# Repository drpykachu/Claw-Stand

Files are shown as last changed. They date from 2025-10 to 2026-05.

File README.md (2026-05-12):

#  Claw Stand

## Hello all! 

This project is inspired by the **BattleBots claw stand robot**:

<div align="center">
  BATTLEBOTS
</div>

---

## Part 1: Mathematical Model

Each finger in the claw contains **3 motors** — **Motor A**, **Motor B**, and **Motor C**.  
Each motor rotates by an angle:  
- Motor A → $\theta_a$  
- Motor B → $\theta_b$  
- Motor C → $\theta_c$  

We need to perform **inverse kinematics** to find the angles needed to position the finger tip at a given **3D coordinate**:

$$(X_p, Y_p, Z_p)$$

<div align="center">
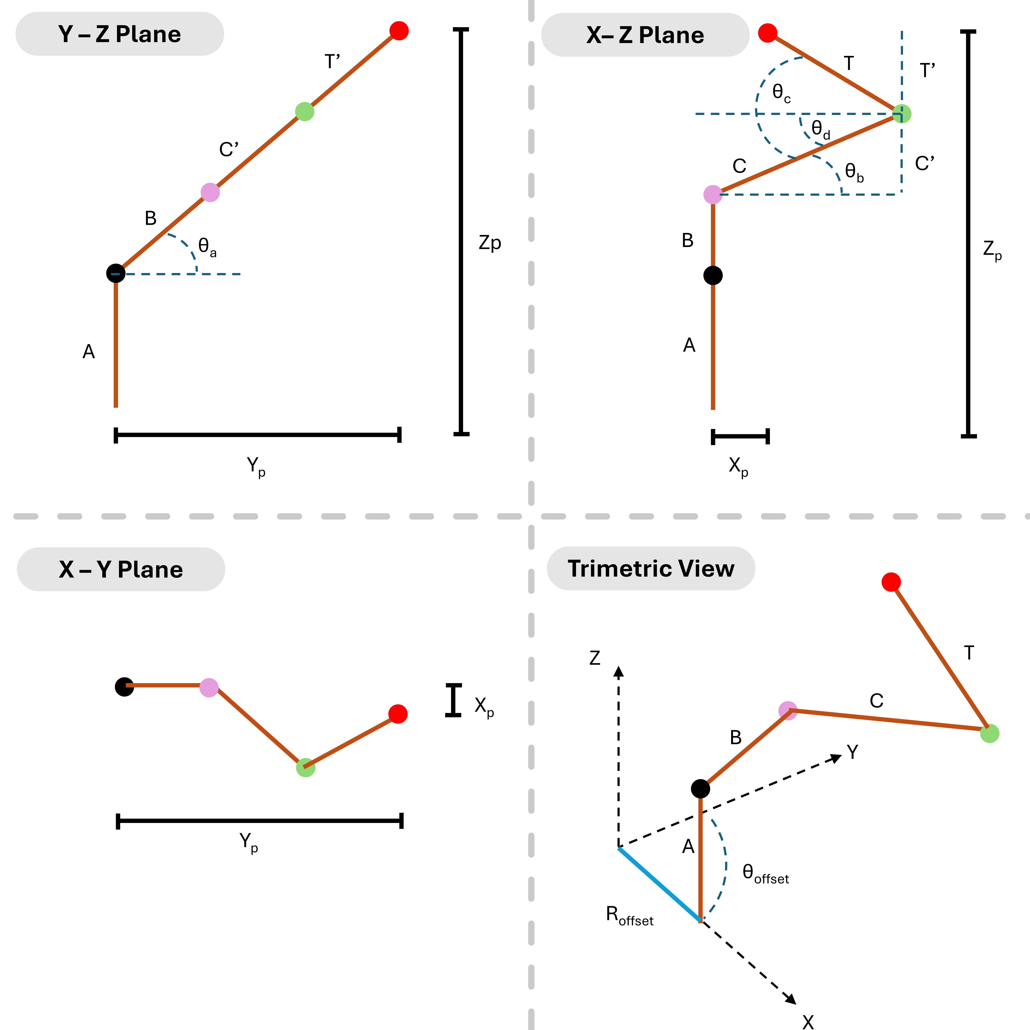
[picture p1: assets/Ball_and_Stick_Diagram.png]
Diagram
  
</div>

---

## Equation Setup

We’re going from a target point in space $(X_p, Y_p, Z_p)$ to joint angles $(\theta_a, \theta_b, \theta_c)$.

$$
\angle AB = \theta_a \quad \angle BC = \theta_b \quad \angle CT = \theta_c
$$

We also define:

$$
\theta_d = \theta_b - \theta_c
$$

---

### Deriving $Z_p$

$$
Z_p = B\sin\theta_a + C'\sin\theta_a + T'\sin\theta_a + A
$$

Substitute: $C' = C\sin\theta_b, \quad T' = T\sin\theta_d $

So:

$$
\boxed{Z_p = B\sin\theta_a + C\sin\theta_b\sin\theta_a + T\sin\theta_d\sin\theta_a + A} \quad \text{(Eq. 1)}
$$

---

### Deriving $Y_p$

$$
Y_p = B\cos\theta_a + C'\cos\theta_a + T'\cos\theta_a
$$

Substitute: $C' = C\sin\theta_b, \quad T' = T\sin\theta_d$

So:

$$
\boxed{Y_p = B\cos\theta_a + C\sin\theta_b\cos\theta_a + T\sin\theta_d\cos\theta_a} \quad \text{(Eq. 2)}
$$

---

### Deriving $X_p$

$$
\boxed{X_p = C\cos\theta_b + T\cos\theta_d} \quad \text{(Eq. 3)}
$$

---

## Step 1 — Solving for $\theta_a$

Visually, this is true from Eq. (1) and Eq. (2):

$$
\tan\theta_a = \frac{Z_p - A}{Y_p}
$$

So:

$$
\theta_a = atan2(\frac{Z_p - A}{Y_p})
$$

#### *Note: atan2 provides the quadrant and is used here, as atan loses information regarding negatives and associated quadrants.
---

## Step 2 — Solving for $\theta_b$ and $\theta_d$

We now solve for $\theta_b$ and $\theta_d$, given:

$$
Y_p = B\cos\theta_a + C\sin\theta_b\cos\theta_a + T\sin\theta_d\cos\theta_a,
$$

$$
X_p = C\cos\theta_b + T\cos\theta_d.
$$

---

### Step 1 — Simplify the equations

Divide the first equation by $\cos\theta_a$ (assuming $\cos\theta_a \neq 0$) and define:

$$
S = \frac{Y_p}{\cos\theta_a} - B.
$$

Then the system becomes:

$$
C\sin\theta_b + T\sin\theta_d = S,  
$$

$$
C\cos\theta_b + T\cos\theta_d = X_p.
$$

---

### Step 2 — Interpret geometrically

These equations represent a **vector addition** in the plane:

$$
C e^{i\theta_b} + T e^{i\theta_d} = X_p + iS \equiv R e^{i\phi},
$$

where

$$
R = \sqrt{X_p^2 + S^2}, \quad \phi = atan2(\frac{S}{X_p}).
$$

---

### Step 3 — Eliminate $\theta_d$

Using the magnitude condition for the complex sum, we find:

$$
X_p\cos\theta_b + S\sin\theta_b = K,
$$

where

$$
K = \frac{R^2 + C^2 - T^2}{2C}.
$$

Let $A = X_p$, $B = S$, and $R = \sqrt{A^2 + B^2}$.
  
Then:

$$
A\cos\theta_b + B\sin\theta_b = K
$$

can be rewritten as:

$$
R\cos(\theta_b - \phi) = K.
$$

---

### Step 4 — Solve for $\theta_b$

$$
\boxed{\theta_b = \phi \pm \arccos\left(\frac{K}{R}\right)}
$$

Feasibility condition:

$$
\left|\frac{K}{R}\right| \le 1.
$$

If \(|K/R| > 1\), no real solution exists.

---

### Step 5 — Solve for $\theta_d$

For each valid $\theta_b$:

$$
\cos\theta_d = \frac{X_p - C\cos\theta_b}{T}
$$

$$
\sin\theta_d = \frac{S - C\sin\theta_b}{T}
$$

$$
\boxed{\theta_d = atan2(\frac{\sin\theta_d}{ \cos\theta_d})}.
$$

---

### Step 6 — Boundary Condition

The result of $\theta_b$ and $\theta_d$ can yield more than one solution. To guarantee that the joints bend outward:

$$
\theta_d > \theta_b
$$

Remembering that $\theta_d = \theta_b - \theta_c$ and substituting:

$$
\theta_c > 0
$$

guarantees a single solution.

---

### Step 7 — Python Implementation

```python
import numpy as np

def solve_thetas(Zp, Yp, Xp, A, B, C, T, Offset_R):
    """Returns the angles (in radians) of motors to obtain a point in space (Xp, Yp, Zp)"""
    Xp = Xp - Offset_R
    Yp = Yp

    # Helps with breakdown of atan2 at infinity as Yp -> 0
    if Yp < 0.0005 and Yp > 0:
        Yp = 0.0005        
    if Yp > -0.0005 and Yp <= 0:
        Yp = -0.0005

    theta_a = np.atan2((Zp-A),Yp)
    ca = np.cos(theta_a)
    
    S = Yp/ca - B
    R = np.hypot(Xp, S)           # sqrt(Xp^2 + S^2)
    phi = np.arctan2(S, Xp)
    K = (R*R + C*C - T*T) / (2.0*C)

    if abs(K/R) > 1.0 + 1e-12:
        return []  # no real solutions

    # clamp for numeric stability
    val = np.clip(K/R, -1.0, 1.0)
    acos_val = np.arccos(val)

    thetab_solutions = [phi + acos_val, phi - acos_val]
    solutions = []
    for tb in thetab_solutions:
        cb = np.cos(tb); sb = np.sin(tb)
        cd = (Xp - C*cb) / T
        sd = (S  - C*sb) / T
        # numeric clamp
        cd = np.clip(cd, -1.0, 1.0)
        sd = np.clip(sd, -1.0, 1.0)
        td = np.arctan2(sd, cd)

        # ensures only one solution
        tc = td - tb

        if tc > 0:
            solutions.append((theta_a, tb, td))
            
    return solutions

```

### Python Model Implementation 

[Model Source Code](https://github.com/drpykachu/Claw-Stand/blob/main/Edition%20V2.0%20-%20Stepper%20Motor/Software/Python/Windows%20-%20Claw%20Stick%20Model%20V2.2.py)

<div align="center">
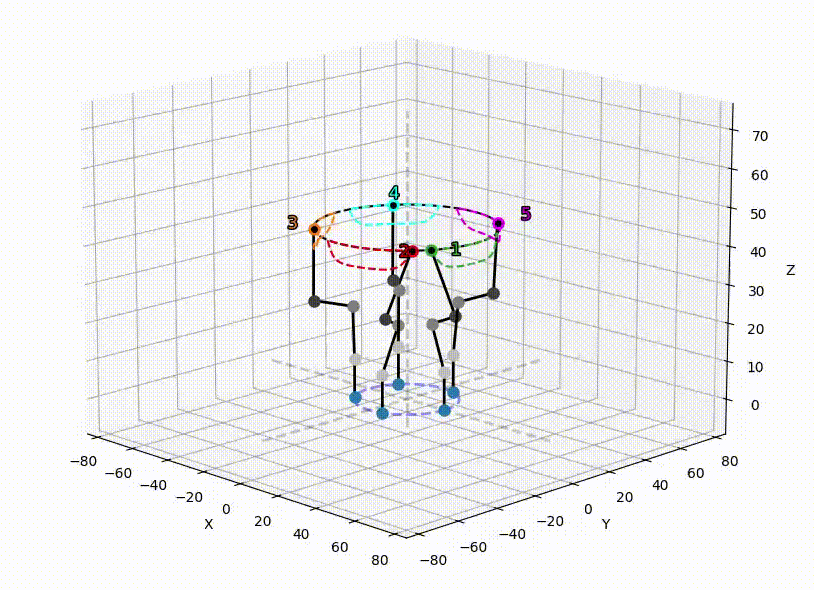
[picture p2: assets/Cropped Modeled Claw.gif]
Python Model
  
</div>

---

## Part 2: Hardware Selection

The angles needed for reaching a point in (x,y,z) space is now fully defined with the mathematical model. However, more thought is needed for selecting the hardware for turning the mathematicl model into a working phyiscal model

---
### The Motor:

There are several classes of motor that were considered, but servo motors are chosen as the range of movement (<180°), built-in rotary encoder (for position tracking and tuning with PID), and step accuracy (the smaller the better) are ideal. Several makes and models of servo motors were evaluated:

* [S8218 High Speed servo](https://www.cysmodel.com/products/cys-s8218-40kg-digital-metal-gear-servo/)
* [SC09 Series Serial Bus Servo](https://www.waveshare.com/SC09-Servo.htm)
* [ST3215 Series Serial Bus Servo](https://www.waveshare.com/st3215-servo.htm?srsltid=AfmBOorEyoYq279kdzu4ZvWRVoV5O3Idv0StNNJXvp_PE0Ioi92Gx9X2)

### Servo Motor Criteria

The three most important criteria for the servo motors to ensure a success build are as follows:

1. Small step angle (as well as compact)
2. Strength requirement (to hold at least coffee mug)

### Step Angle

The Ball-And-Stick model has the oversight of showing us how the model would react with perfect decimal-point accuracy. In the real world, motors have an angle, the step angle or resolution angle, of how small they can exert movement in discrete steps. For instance, a large step can lead to unwanted behavior. A Computer Aided Design (CAD) was built for the SC09 motors, where the components were designed in mind for 3D printing later on. The model with a 2° step is seen here (notice the choppiness and inaccurate positioning on the the wanted path):

<div style="display: flex; justify-content: center;">
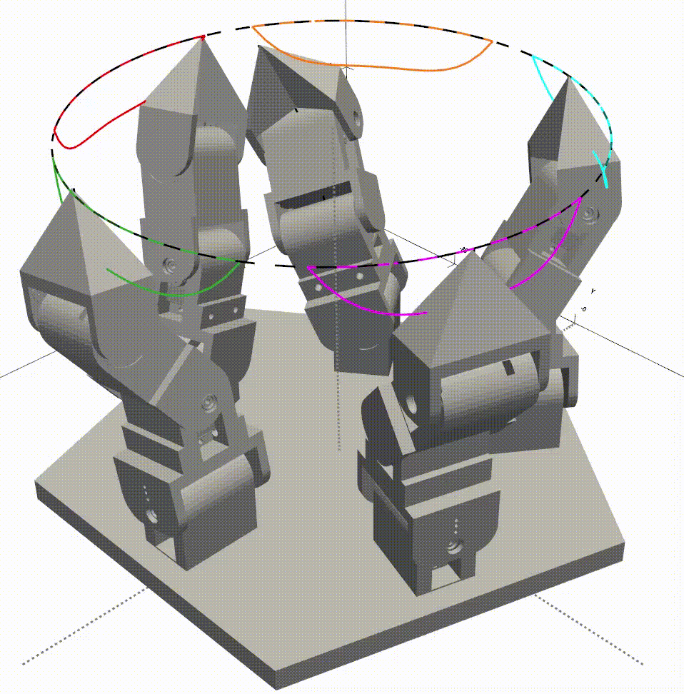
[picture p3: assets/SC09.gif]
  
</div>

<br>

Choppiness and innacuracy of the fingers is seen, indicating that there will be poor movement and stability. A smaller step angle is needed to ensure smooth control. 

The smallest step angle size and  10x step angle size (closer to actual movement due to internal deadband settings), is seen for each motor below:

| Make | Min Step Size  | Acutal Step Size | 
|---|---|---|
| S8218 | 0.360 | 3.60 |
| SC09 | 0.293 | 2.93 | 
| ST3215  | 0.088 | 0.88 |

A CAD model for the ST3215 was to show the operation for a 0.88° step angle, where much better control smoothness is observed:

<div style="display: flex; justify-content: center;">
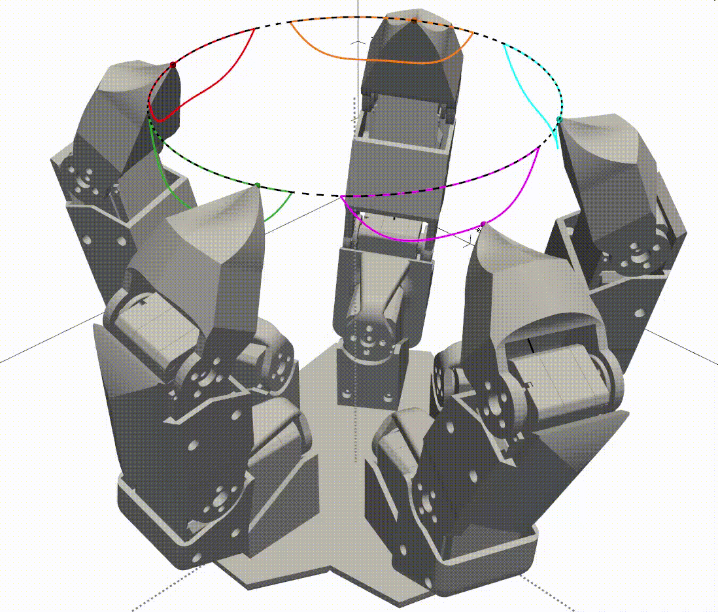
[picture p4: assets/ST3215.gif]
  
</div>

The S8218 and SC09 motors were no longer considered as they show poor control for this configuration.

### Strength Requirement
The ST3215 achieves its positional accuracy by using a gearbox. Gearboxes are good for increasing torque (strength) and increasing position resolution, but they are bad because they introduce *backlash*. Backlash is the clearance or lost motion in a mechanism caused by gaps between the parts. If there was no clearance between the gears, any anamoly would cause the gearbox to seize - causing lack or no motion and potential motor failure; so some backlash is desired. However, backlash in this system means that the rotor can move without the output shaft moving, causing a displacement between the modeled position and the actual position (*bad*).

Here is a picture depicting backlash:

<div align="center">
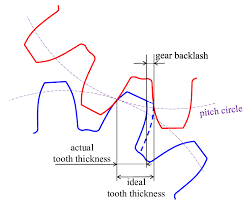
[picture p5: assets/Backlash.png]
Backlash
  
</div>

Only one side of the gear teeth is engaged at a time. Once the gears spin the other direction, there will be a moment in time (and space) where the contact has to shift from one side to the other. However, if a sufficient amount of external torque is applied, one side of the gear will be engaged at all times - and therefore eliminating backlash.

Looking at bottom motor (Motor A) for example, gravity will pull the gearings to one side, until 90 degrees, where it will slop over to the other side. Assigning positive torque to a clockwise direction (and thus a negative torque is counter clockwise), the moment ($\tau$) associated for each motor is found as:

$$\tau = \sum_{i=1}^{n} l_i·m_i·g·cos(\theta) + l_L·m_L·g·cos(\theta); $$

$$\tau_C = [T·(m_{p,T})]·g·cos(\theta) + T·m_L·g·cos(\theta)$$

$$\tau_B = [T·(m_{p,T}) + (T+C)·(m_{p,T}+m_{p,C}+m_{m})]·g·cos(\theta) + (T+C)·m_L·g·cos(\theta)$$

$$\tau_A = [T·(m_{p,T}) + (T+C)·(m_{p,T}+m_{p,C}+m_{m}) + (T+C+B)·(m_{p,T}+m_{p,C}+m_{p,B}+ 2m_{m})]·g·cos(\theta) + (T+C+B)·m_L·g·cos(\theta) $$

where $l_i$ is arm length, $l_L$ is load length, $m_{p}$ is mass of plastic, $m_{m}$ is mass of motor, $m_{L}$ is mass of load, and $g$ is gravity. Note that the moments $\tau_B$ and $\tau_A$ are taken as worst-case scenarios of the finger being fully extended.

The torque vs. angle behavior, where the load is only applied during contact with the plate,
is seen here: 

<div align="center">
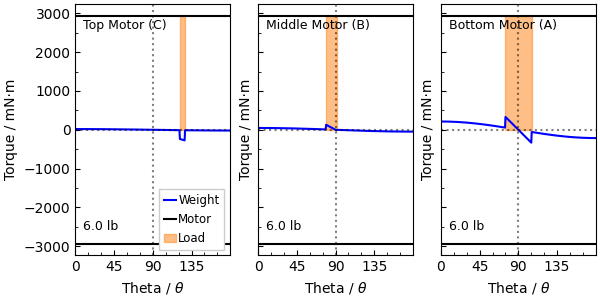
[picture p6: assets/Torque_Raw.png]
Torque_Raw
  
</div>

My father chimed in at this point to point out that the torque measurment only needs to be considered for motors that have angles cross the 90° mark. This agrees with the point that as long there is no change in sign (+/-) of torque, there is no switch over from one gearing side to the other. Thus, motors C and B are removed from further analysis.

An additional torque will be needed to have the gears stay on one side for motor A. A torsion spring will be added to raise the torqe as a function of the angle, with the relationship seen as:

$$\tau_S = K_s\theta$$

The torque increased with the angle moved (assuming a 270° spring deflection) so that the gears are preloaded the angle reaches 90°. The torque behavior with the added spring is seen as:

<div align="center">
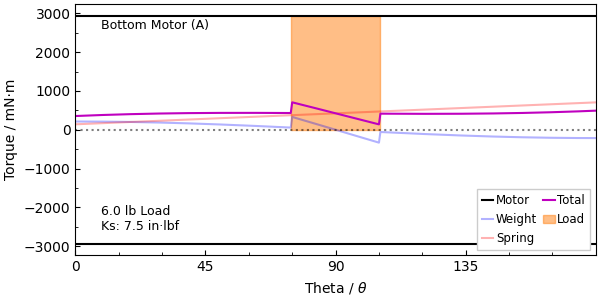
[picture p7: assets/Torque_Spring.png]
Torque_Spring
  
</div>

The torque is now brought to one side (positive) and remains there for all angles - ensuring that the gears are continuously in contact. Motors A, B, and C are now fully defined. The final model to include the spring hardware (near the bottom, as only motor A needs it) is seen here:

<div style="display: flex; justify-content: center;">
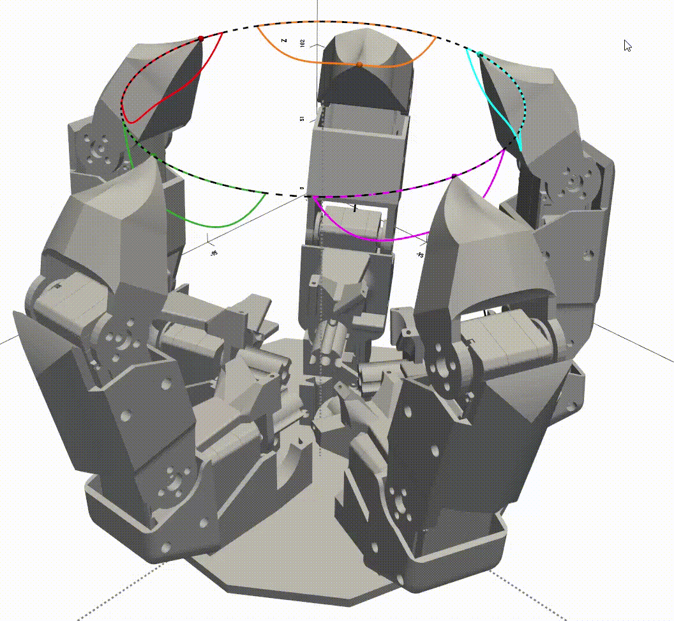
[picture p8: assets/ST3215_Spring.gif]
  
</div>

## Part 3: Final Build And Considerations

The translation from theoretical model, to CAD model, to 3D printing and fine-tuning took a considerable amount of time and effort. The considerations for electronics, wiring, polishing, machining, soldering, and coding are not shown here, simply because it is not worth the time and effort type of out the explanations for each aspect. Rather, I wanted to share the aspects to which I thought were the neat.

### Electronics Bay

The fingers that comprise the claw in the presented animations are connectec to a base plate. I chose to make an electronics bay that houses the computer, power supplies, and other ancillary electronics equipment to make the claw a stand-alone piece. The processor chosen to run the claw computations and motor control commands is a Easpberry Pi 5. The motor driver is a 12v serial bus driver. The Pi requires a 5V power supply, and the motor driver require a 12V supply, which are included in the bay as well. Lastly, I included a ring of LED that is oriented upwards to illuminate the object being held. 

<div align="center">
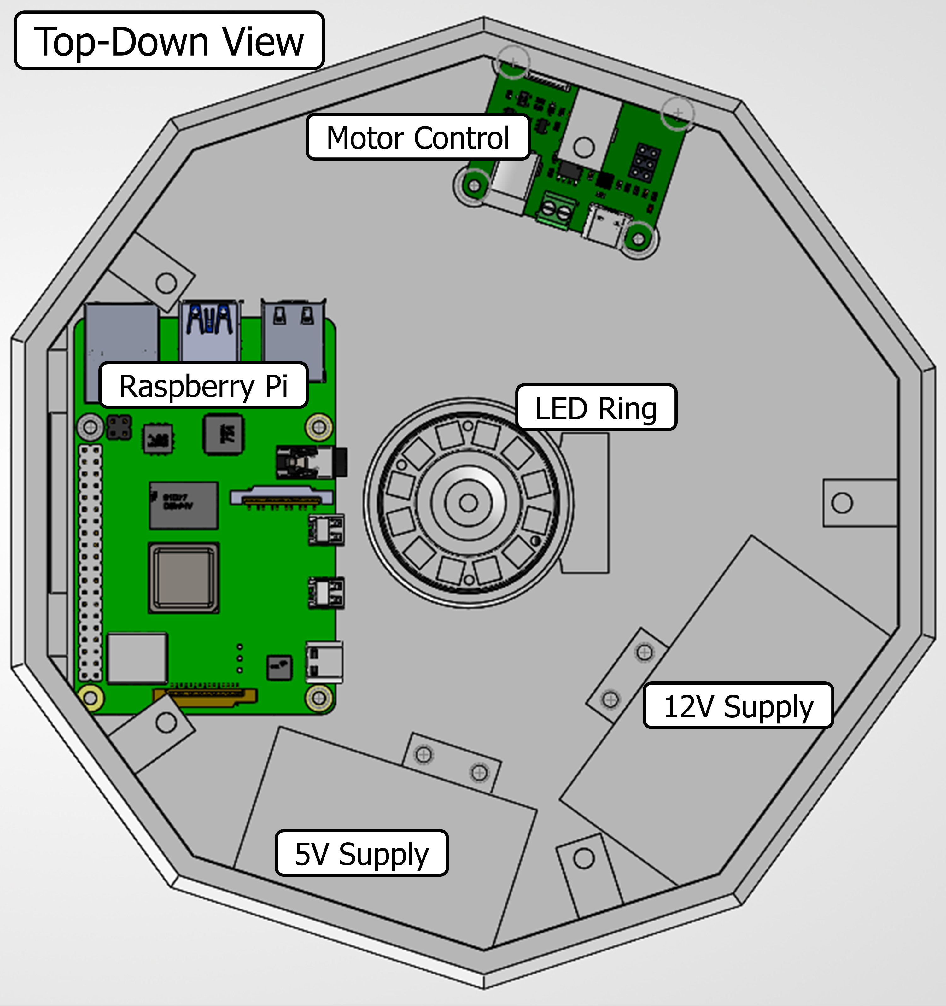
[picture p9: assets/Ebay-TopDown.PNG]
Ebay-TopDown
  
</div>
 
<br>
<div align="center">
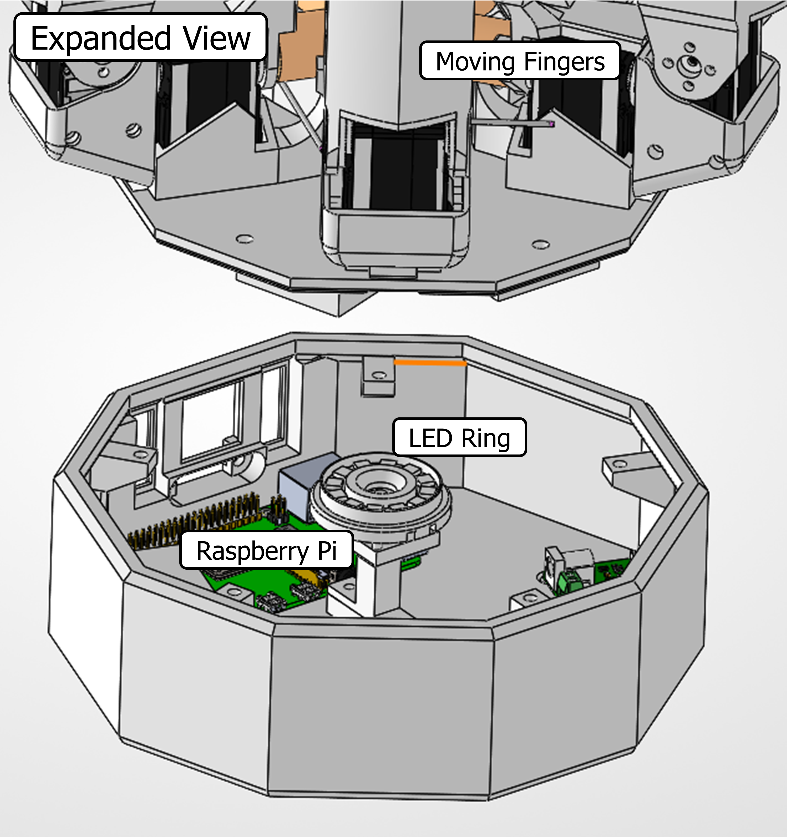
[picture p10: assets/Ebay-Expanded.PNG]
Ebay-Expanded
  
</div> 

<br>

### Camera-Plate Feedback Loop

The claw, finally completed and ready to run, was initially only able to hold spherical objects as they are symmetrical in any orientation. Any spherical object would auto-correct if there was any mis-calibration in fingertip position. Holding other types of objects, such as flat objects (plate), would be a challenge as any fingertip position mis-calibration would lead to drift. Enough drift, and the plate falls off the plate. With the addition of a small raspberry pi camera, along with the processing power of the Raspberry Pi and the ulimtation aspect of the LED ring, image processing feedback loop was developed to track the location of plate. If the plate drifted too far to one side, the raspberry pi goes into "fixing mode" to bring the plate back to near center. *Development of this image correction hardware and software took by far the longest amound of time to make*

The animation of a drift detection and correction is seen here:

<div style="display: flex; justify-content: center;">
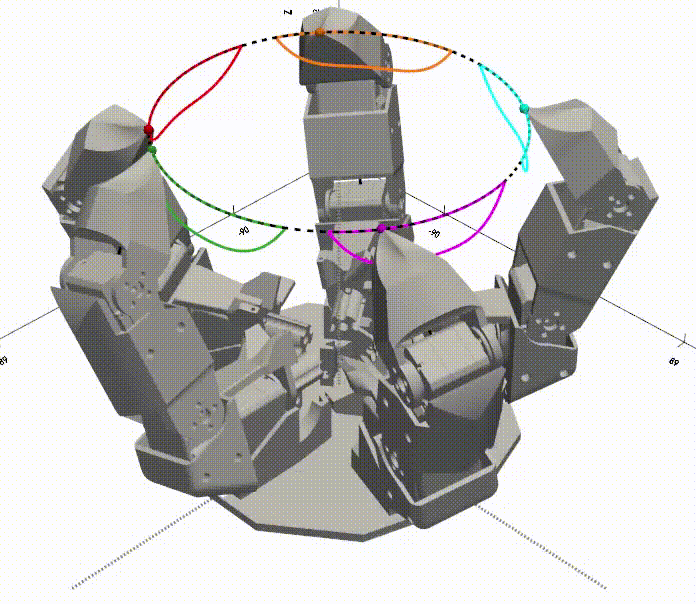
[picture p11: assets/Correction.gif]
Correction
  
</div>

<br>
Where the dashed black line is the normal path to follow, and the gray curve is the correction path. When a drift threshold is met (15 mm from center), the all fingers move in sync to move the plate back to the center. After the translational movement, the fingers need to reset their position from the correction path to the normal path. I first attempted to hold each finger still and move one at a time, but there were instances of imbalance between fingers due to the position on the path, and the the plate would fall off. The resetting of the fingers in this animation differs from the former by having the finger position reset during the downsweep. This is observed by a finger leaving on the dashed gray circle during the start of the downsweep, and touching the dashed black circle on the end of the downsweep.

## Gallery

### Electronics Bay

<div align="center">
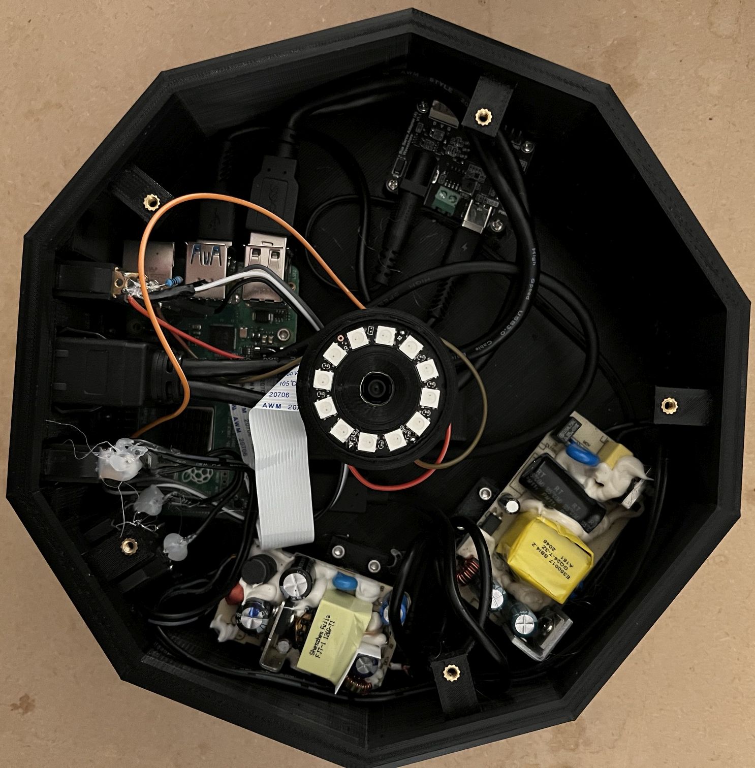
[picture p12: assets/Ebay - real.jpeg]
Ebay-real
  
</div> 

<br>

### Claw - Stagnant

<div align="center">
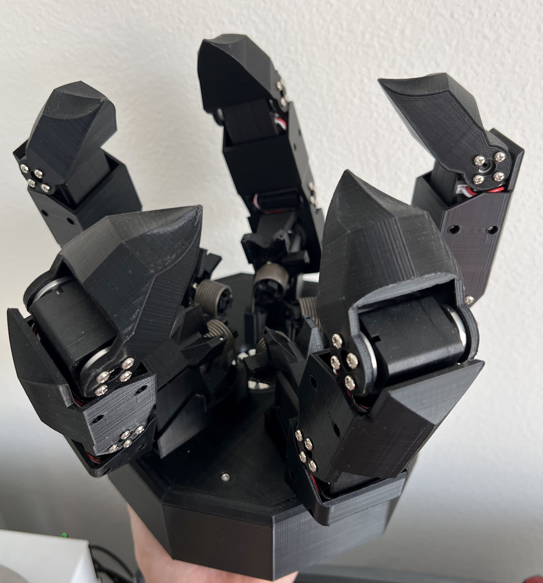
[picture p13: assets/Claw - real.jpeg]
Claw-real
  
</div> 

<br>

### Claw - Moving

<br>

https://github.com/user-attachments/assets/a1c54686-66d3-4b85-84ab-2f56ab6c1aae

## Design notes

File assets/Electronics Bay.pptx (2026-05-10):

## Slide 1

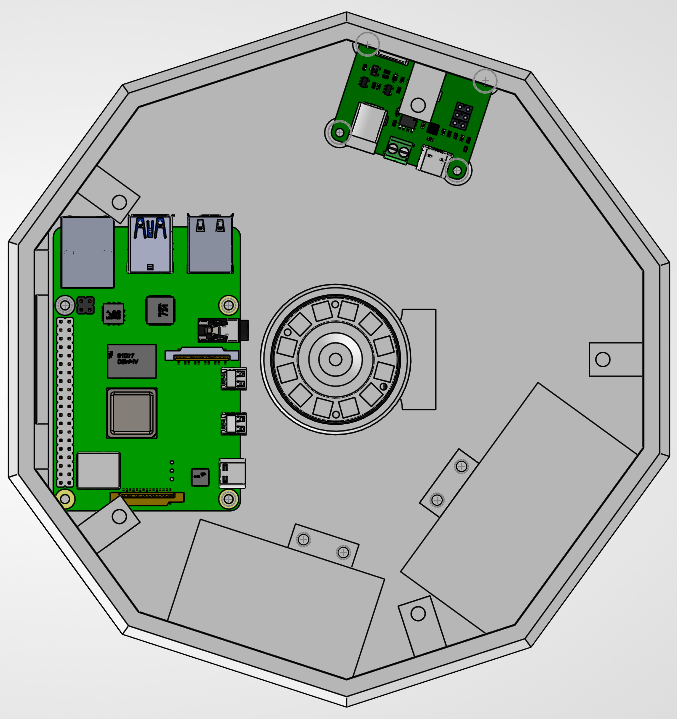
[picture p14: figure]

Top-Down View

Motor Control

Raspberry Pi

LED Ring

12V Supply

5V Supply

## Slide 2

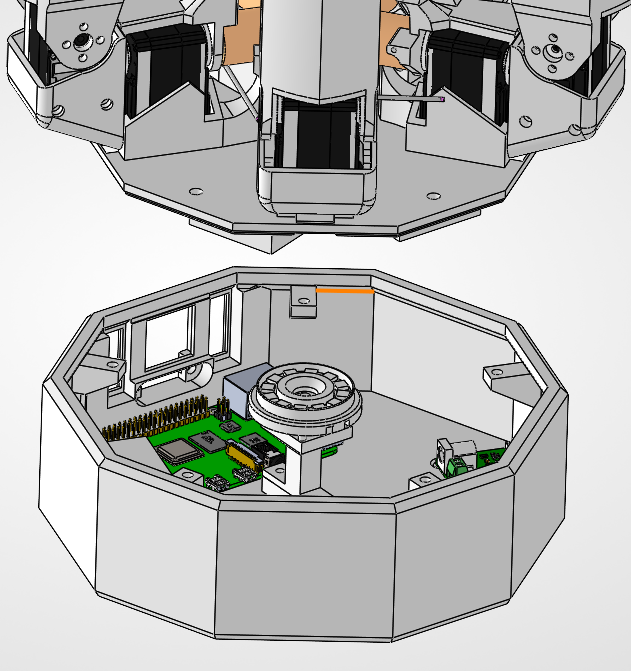
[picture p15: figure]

Expanded View

Moving Fingers

LED Ring

Raspberry Pi

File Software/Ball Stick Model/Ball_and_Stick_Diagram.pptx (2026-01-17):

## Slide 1

Y – Z Plane

T’

X– Z Plane

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
X – Y Plane

Trimetric View

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
θoffset

Roffset

X

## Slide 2

Y – Z Plane

T’

X– Z Plane

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
X – Y Plane

Trimetric View

Yp

Z

T

Xp

θoffset

B

Y

C

A

Roffset

X

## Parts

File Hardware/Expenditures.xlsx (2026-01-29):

Index | Item | Amount needed | Quantity in Unit | Units needed | Cost per unit | Total Cost | Item Type | Used in Final | Link
1 | Raspberry Pi 4 Model B Kit | 1 | 1 | 1 | 119.99 | 119.99 | Logic | Yes | https://www.amazon.com/dp/B07XTQL6YZ?ref=ppx_yo2ov_dt_b_fed_asin_title&th=1
2 | Raspberry Pi Camera Module 3 | 1 | 1 | 1 | 18.5 | 18.5 | Logic | Yes | https://www.amazon.com/Arducam-Raspberry-Camera-Autofocus-15-22pin/dp/B0C9PYCV9S
3 | Powered USB Hub (<3 ports) | 1 | 1 | 1 | 7.99 | 7.99 | Logic | No | https://www.amazon.com/RSHTECH-Splitter-Portable-Aluminum-Individual/dp/B07HMZSRS7
4 | ESP32 DevkitC | 1 | 3 | 1 | 17.97 | 17.97 | Logic | Yes | https://www.amazon.com/ESP32-DevKitC-32-Development-Supporting-Bluetooth-Interface/dp/B0DYDN5X1Z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
5 | USB C cables | 1 | 5 | 1 | 7.99 | 7.99 | Logic | No | https://www.amazon.com/Android-Compatible-Smartphones-Charging-Stations/dp/B095JZSHXQ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
6 | 28BYJ-48 ULN2003 5V Stepper Motor + ULN2003 | 5 | 5 | 1 | 14.99 | 14.99 | Motor | No | https://www.amazon.com/28BYJ-48-ULN2003-Stepper-Driver-Arduino/dp/B07YRHX73L
7 | Female to Female Breadboard Jumper Wires | 120 | 120 | 1 | 7.98 | 7.98 | Motor | No | https://www.amazon.com/dp/B07GCY6CH7?ref=ppx_yo2ov_dt_b_fed_asin_title
8 | 5 V 8–10 A Regulated DC Power Supply | 1 | 1 | 1 | 14.99 | 14.99 | Power | No | https://www.amazon.com/PHEVOS-Universal-Switching-Raspberry-Computer/dp/B07H5Q2PC2?hvadid=694085195674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
9 | PSU Capacitor | 1 | 2 | 1 | 7.99 | 7.99 | Power | No | https://www.amazon.com/Cermant-100v-3-3uf-Electrolytic-Non-Polarized/dp/B0CZP2Q26M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
10 | C14 Panel Mount Plug Adapter | 1 | 2 | 1 | 7.79 | 7.79 | Power | Yes | https://www.amazon.com/dp/B07PVP7GL2?ref=ppx_yo2ov_dt_b_fed_asin_title&th=1
11 | 4-40 bolts | 5 | 100 | 1 | 6.27 | 6.27 | Structure | Yes | https://www.amazon.com/dp/B0F93L5MJK?ref=ppx_yo2ov_dt_b_fed_asin_title
12 | 4-40 threaded inserts | 5 | 100 | 1 | 11.02 | 11.02 | Structure | Yes | https://www.amazon.com/dp/B0DY6P1K41?ref=ppx_yo2ov_dt_b_fed_asin_title
13 | 12V power supply | 1 | 1 | 1 | 8.46 | 8.46 | Power | Yes | https://www.amazon.com/dp/B0D476TCVW?ref=ppx_yo2ov_dt_b_fed_asin_title
14 | Stepper motor driver | 1 | 1 | 1 | 13.23 | 13.23 | Motor | No | https://www.amazon.com/dp/B0CP92T4QR?ref=ppx_yo2ov_dt_b_fed_asin_title
15 | Stepper motor driver | 1 | 1 | 1 | 17.64 | 17.64 | Motor | No | https://www.amazon.com/dp/B0832SK397?ref=ppx_yo2ov_dt_b_fed_asin_title
16 | Power supply adjustable | 1 | 1 | 1 | 48.21 | 48.21 | Tool | No | https://www.amazon.com/dp/B0D2TLJP3D?ref=ppx_yo2ov_dt_b_fed_asin_title
17 | Flanged bushings | 1 | 1 | 1 | 7.16 | 7.16 | Structure | No | https://www.amazon.com/dp/B0FHQ63MS3?ref=ppx_yo2ov_dt_b_fed_asin_title
18 | ST09 Servos | 3 | 1 | 3 | 15.99 | 47.97 | Motor | No | https://www.amazon.com/dp/B0C3QGLGB8?ref=ppx_yo2ov_dt_b_fed_asin_title
19 | Servo driver | 1 | 1 | 1 | 19.19 | 19.19 | Logic | Yes | https://www.amazon.com/dp/B0D1R4SGFS?ref=ppx_yo2ov_dt_b_fed_asin_title&th=1
20 | ST3215 Servo | 15 | 1 | 15 | 26.99 | 404.85 | Motor | Yes | https://www.amazon.com/dp/B0FKY4Z15R?ref=ppx_yo2ov_dt_b_fed_asin_title
21 | PLA Filament | 1 | 1 | 1 | 14.91 | 14.91 | Structure | Yes | https://www.amazon.com/your-orders/orders?startIndex=0&ref_=ppx_yo2ov_dt_b_pagination_2_1
 |  | Breakdown:
 |  | Category | Cost
 |  | Logic | 191.63
 |  | Motor | 506.66
 |  | Power | 39.23
 |  | Structure | 39.36
 |  | Tool | 48.21
 |  | Total | 825.09
 |  | Perfect | 628.95
 |  | Learning | 196.14

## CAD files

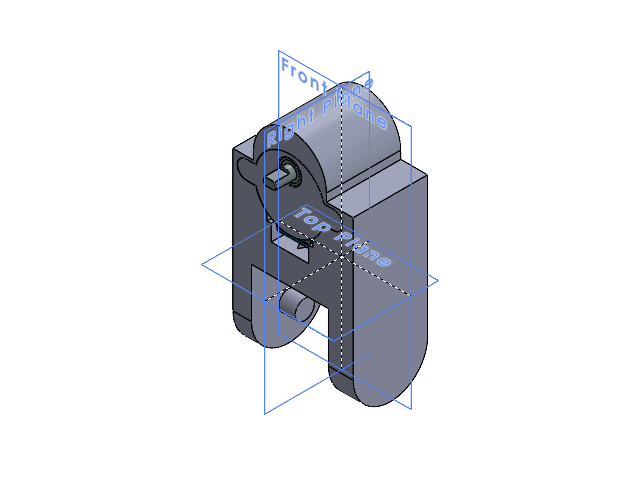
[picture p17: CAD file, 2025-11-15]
Hardware/3D Models/28BYJ-48/Sub Assemblies/Motor B + bearing.SLDASM
Motor B
Bearing
28BYJ-48
Motor Holder
Bearing Insert

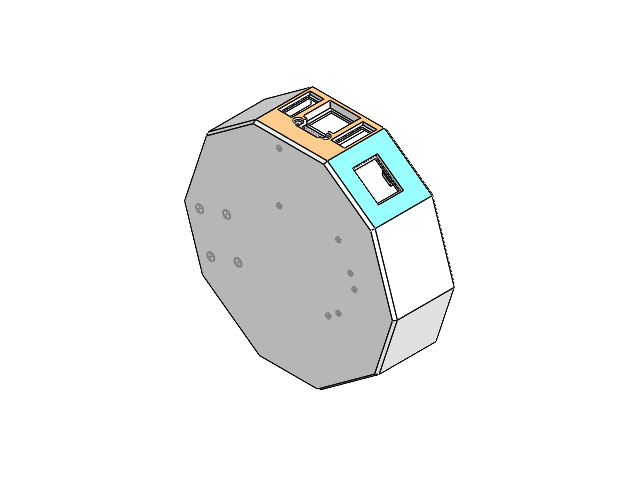
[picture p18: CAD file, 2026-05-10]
Hardware/3D Models/ST3215/V1.0/ST3215_Assembly_Electronics_Bay.SLDASM
ST3215_Electronics_Bay
5V_Supply
5V_Base_Connector
12V_Base_Connector
12V_Supply
Bus Servo Adapter (A)
Raspberry Pi 4 Model B
Camera_Base_Glue
Camera_Base_Screw
arducam
Camera_Hole
WS2812 LED Ring

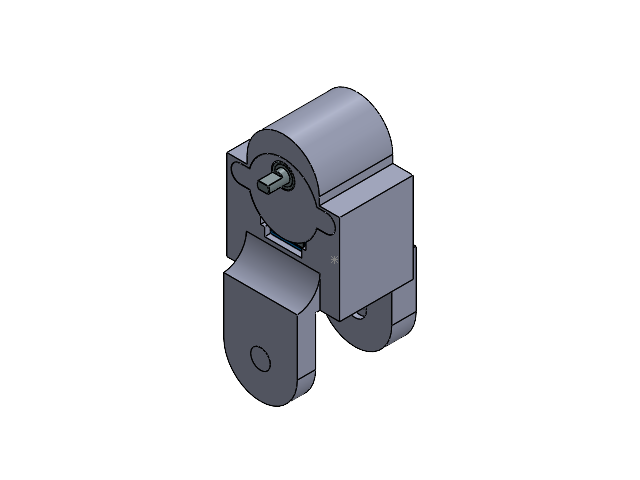
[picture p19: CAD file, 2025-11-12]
Hardware/3D Models/28BYJ-48/Sub Assemblies/Motor C + bearing.SLDASM
Motor C
28BYJ-48
Bearing
Motor Holder

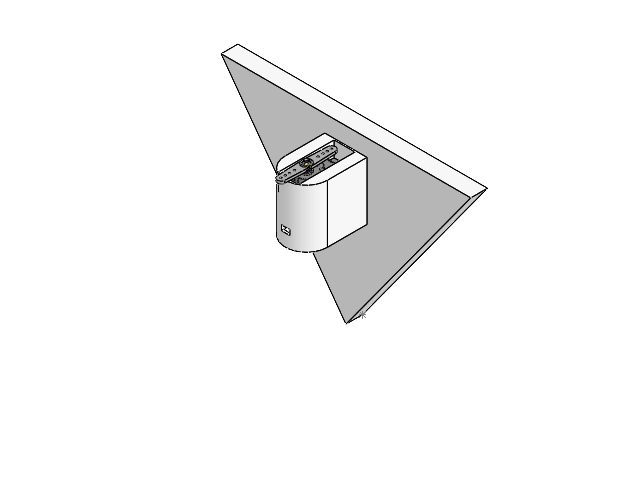
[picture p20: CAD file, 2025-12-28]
Hardware/3D Models/SC09/V0.1 - Bearing/SC09_Holder_Motor_A_Python.SLDASM
SC09_Holder_Motor_A
SC09-SERVO
SC09_Servo_Connector

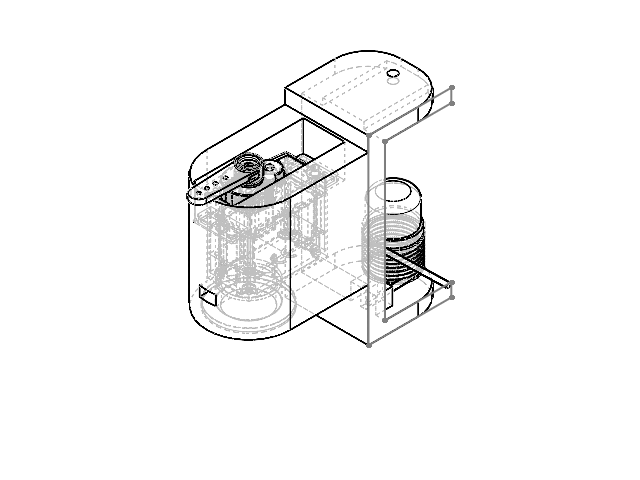
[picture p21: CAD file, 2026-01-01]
Hardware/3D Models/SC09/V0.2 - Bushing & Spring/SC09_Holder_Motor_C_Python.SLDASM
SC09-SERVO
SC09_Servo_Connector
SC09_Holder_Motor_C
9271K382_Torsion Spring
Bushing

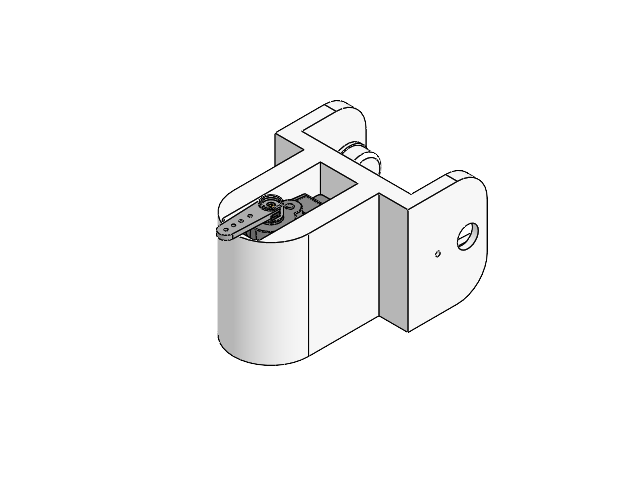
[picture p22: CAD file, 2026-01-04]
Hardware/3D Models/SC09/V0.2 - Bushing/SC09_Holder_Motor_B_Python.SLDASM
SC09-SERVO
SC09_Servo_Connector
SC09_Holder_Motor_B
Bushing

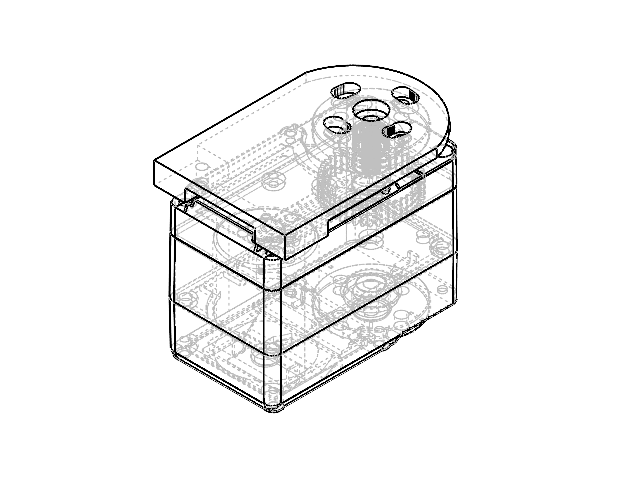
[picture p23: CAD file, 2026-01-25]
Hardware/3D Models/ST3215/Motor Debugging/CenterFinder_Test.SLDASM
CenterFinder
ST3215

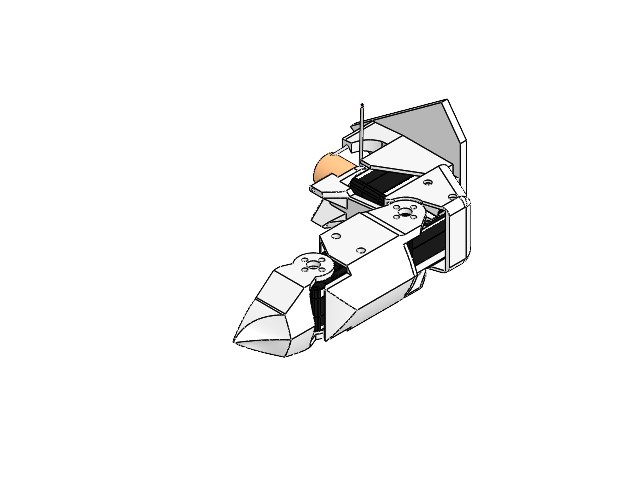
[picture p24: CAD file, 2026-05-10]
Hardware/3D Models/ST3215/V1.0/ST3215_Assembly_Finger.SLDASM
ST3215_Holder_A
ST3215 x 3
ST3215_Holder_B
ST3215_Holder_C
ST3215_Holder_A_Arm_Cut1
ST3215_Holder_A_Arm_Cut2
9271K581_Torsion Spring
ST3215_Holder_A_Arm_Cut3

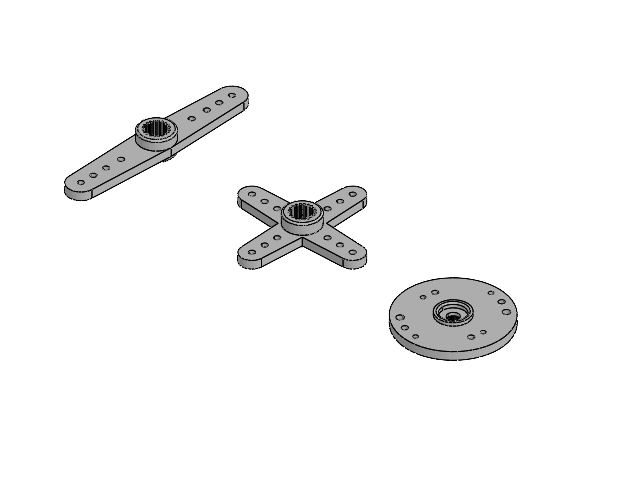
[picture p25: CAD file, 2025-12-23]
Hardware/3D Models/SC09/V0.1 - Bearing/Imports/SC09_ARM.SLDASM
SJ-BB00-0024-CYCLE-0716_9.step
SJ-BB00-0026-ONEARM-0716_16.step
eBom-FreeParts.step

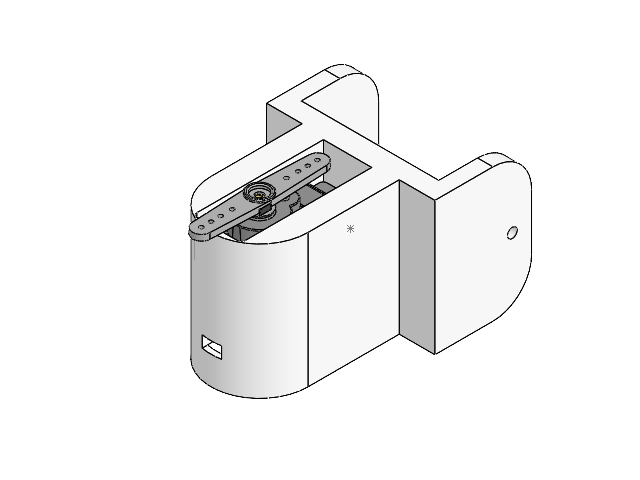
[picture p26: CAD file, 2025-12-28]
Hardware/3D Models/SC09/V0.1 - Bearing/SC09_Holder_Motor_B_Python.SLDASM
SC09-SERVO
SC09_Servo_Connector
SC09_Holder_Motor_B

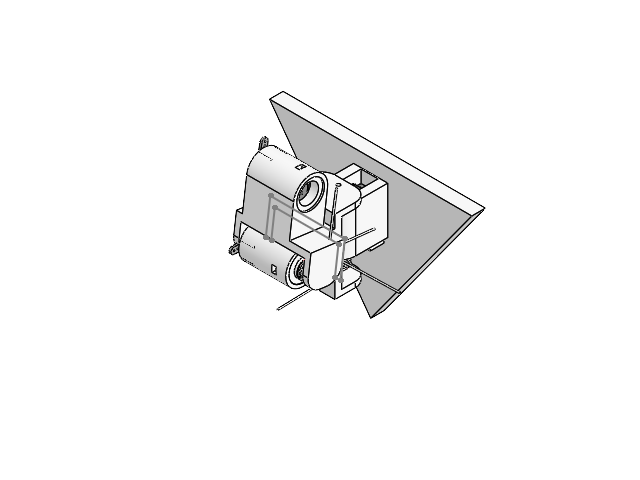
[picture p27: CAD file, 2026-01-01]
Hardware/3D Models/SC09/V0.2 - Bushing & Spring/SC09_Assembly_ABC.SLDASM
SC09_Holder_Motor_A
SC09-SERVO x 3
SC09_Servo_Connector x 3
Bushing x 2
SC09_Holder_Motor_B
9271K382_Torsion Spring x 2
SC09_Holder_Motor_C

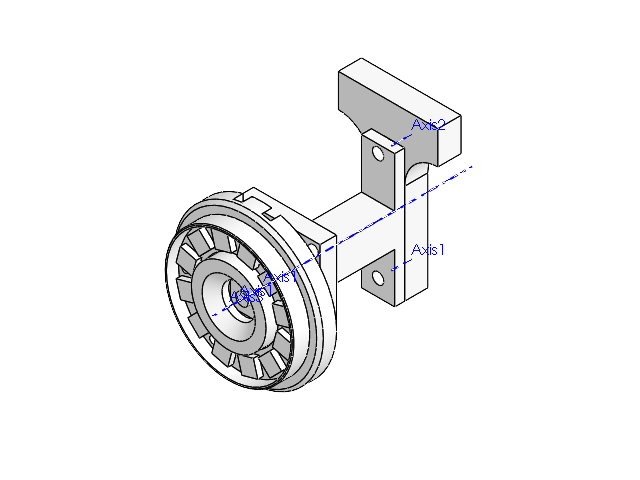
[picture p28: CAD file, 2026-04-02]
Hardware/3D Models/ST3215/V1.0/Camera/Camera_Holder.SLDASM
Camera_Base_Glue
Camera_Base_Screw
arducam
Camera_Hole
WS2812 LED Ring

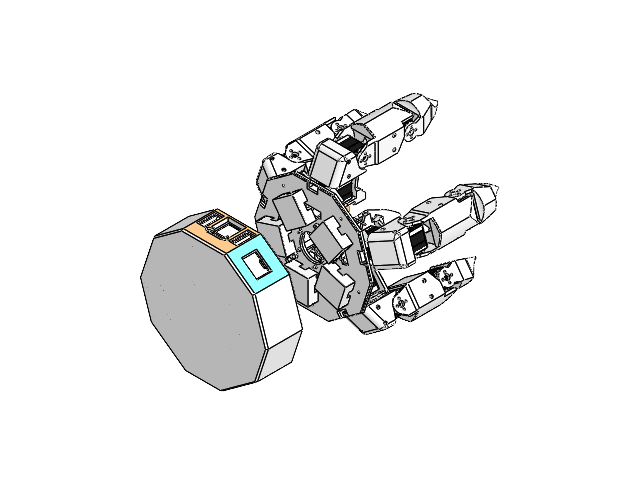
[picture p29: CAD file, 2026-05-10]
Hardware/3D Models/ST3215/V1.0/ST3215_Assembly_ALLCOMPLETE.SLDASM
ST3215_Holder_A_Base
ST3215 x 15
ST3215_Holder_B x 5
ST3215_Holder_C x 5
ST3215_Holder_A_Arm_Cut1 x 5
ST3215_Holder_A_Arm_Cut2 x 5
9271K581_Torsion Spring x 5
ST3215_Holder_A_Arm_Cut3 x 5
ST3215_Electronics_Bay
5V_Supply
5V_Base_Connector
12V_Base_Connector
12V_Supply
Bus Servo Adapter (A)
Raspberry Pi 4 Model B
Camera_Base_Glue
Camera_Base_Screw
arducam
Camera_Hole
WS2812 LED Ring
ST3215_MotorJunctin_Bay x 5

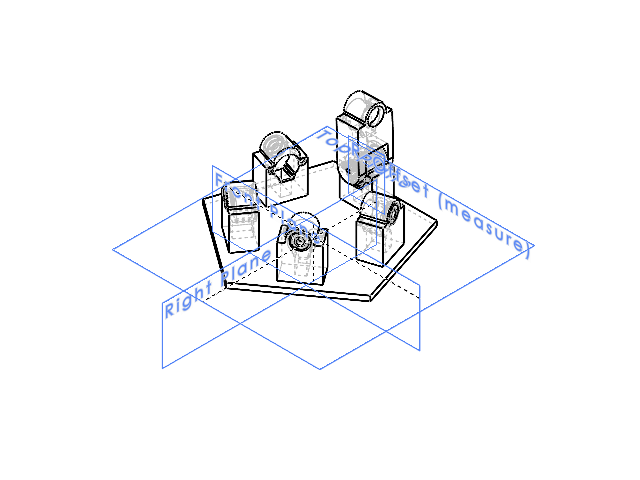
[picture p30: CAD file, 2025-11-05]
Hardware/3D Models/28BYJ-48/Sub Assemblies/Motor A + bearing + base.SLDASM
Motor A + Base
Bearing x 5
28BYJ-48
Motor B
Motor Holder

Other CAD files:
Hardware/3D Models/SC09/V0.1 - Bearing/SC09_Holder_Motor_T_Python.SLDASM
Hardware/3D Models/SC09/V0.1 - Bearing/SC09_Holder_Motor_C_Python.SLDASM
Hardware/3D Models/SC09/V0.2 - Bushing & Spring/SC09_Assembly_Main.SLDASM
Hardware/3D Models/SC09/V0.2 - Bushing & Spring/SC09_Assembly_AB.SLDASM
Hardware/3D Models/28BYJ-48/28BYJ-48.SLDPRT
Hardware/3D Models/28BYJ-48/Bearing Insert.SLDPRT
Hardware/3D Models/28BYJ-48/Bearing.SLDPRT
Hardware/3D Models/28BYJ-48/Imports/28BYJ-48.SLDPRT
Hardware/3D Models/28BYJ-48/Imports/Raspberry Pi 4 Model B.SLDPRT
Hardware/3D Models/28BYJ-48/Imports/Step/28BYJ-48+ULN2003A Step Motor Module.SLDPRT
Hardware/3D Models/28BYJ-48/Imports/Step/28BYJ-48+ULN2003A Step Motor Module.stp
Hardware/3D Models/28BYJ-48/Imports/ULN2003A.SLDPRT
Hardware/3D Models/28BYJ-48/Motor A + Base.SLDPRT
Hardware/3D Models/28BYJ-48/Motor B.SLDPRT
Hardware/3D Models/28BYJ-48/Motor C.SLDPRT
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

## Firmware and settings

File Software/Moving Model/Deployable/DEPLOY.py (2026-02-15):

import time
import numpy as np
from st3215 import ST3215
from DEPLOY_FUNCTIONS import * # Home brew package


# ======================================================= Parameters =========================================================

# Digit Lengths
A = 45 # bottom digit + motor A height
A_x = 39.8
B = 19.8 # lower-middle digit + motor B height

C = 75 # upper-middle middle 2 digit + motor B height
T = 65 # top digit height

num_fingers = 5

Offset_R    = 60.075  # From origin (0,0,0)

R_tar       = 80  # Radius of target circle path 
H_tar       = 190  # Height of target circle path


delta_Z     = 20   # Dropping from path for reset 
points      = 200  # Number of points for path
speed       = 100   # Animation speed

# ================= Pathing ===================
Offset_theta_master = np.linspace(360,0,num_fingers+1)[0:num_fingers] # Flip the 0 and 360 to change direction
circle_tar = circle(R_tar, H_tar, np.linspace(0, 359, points))        # Builds target circle
fingertip_path = pathing(points, delta_Z,num_fingers,R_tar, H_tar)    # Builds a fingertip path
master_path = patterns('Roll',num_fingers, points,fingertip_path)

# ======================================================= Motor Connections =========================================================

try:
    # Establishes motor communication
    servo = ST3215('COM15')
    servo_dict = {}
    for i in range(num_fingers):
        servo_dict[f'F{i+1}_A'] = 10*i+0+10
        servo_dict[f'F{i+1}_B'] = 10*i+1+10
        servo_dict[f'F{i+1}_C'] = 10*i+2+10
    
    servo_here = []
    print('Available Servos:')
    for servo_ping in servo_dict:
        if servo.PingServo(servo_dict[servo_ping]): 
            servo_here.append(servo_ping)
    print(servo_here)
    
    #### Centers Motors ####
    center_A_C = 2048
    center_B   = 2048
    for motors in servo_here:
        if motors[-1] == 'B':
            servo.MoveTo(servo_dict[motors], center_B)
        else:
            servo.MoveTo(servo_dict[motors], center_A_C)
            
    #### Sets Motor Speed ####
    motor_speed = 4096
    for motors in servo_here:
        servo.SetSpeed(servo_dict[motors], motor_speed)
    motors_found = True

except:
    print('No motors available')
    motors_found = False





minmax_a = []
minmax_b = []
minmax_c = []
# Initial check - finds max angle and steps

for i in range(points):
    Xtar, Ytar, Ztar = master_path[0, :, int(i)]
    try:
        theta_a,theta_b,theta_c = solve_thetas(Ztar, Ytar, Xtar, A, A_x, B, C, T,Offset_R)[0]
        minmax_a.append(theta_a)
        minmax_b.append(theta_b)
        minmax_c.append(theta_c)
    except Exception as e:
        print('\033[91m EXITING - not all points in path have a solution.\033[0m')
        sys.exit(1)





val_motor = 0

def animate():
    global val_motor

    if val_motor == points:
        val_motor = 0
            
    #### Updates Motor movement

        
    for k in range(num_fingers):
        ### Finding angles and rebuilding fingers
        Xtar, Ytar, Ztar = master_path[k, :, int(val_motor)] 
        Offset_theta = Offset_theta_master[k]
        Xtar_new, Ytar_new = rotate_point((0,0), (Xtar, Ytar),Offset_theta)
        Ztar_new = Ztar
        
        theta_a, theta_b, theta_c = solve_thetas(Ztar, Ytar, Xtar, A, A_x, B, C, T,Offset_R)[0]             
        if motors_found and ok:
            servo.MoveTo(servo_dict[f'F{k+1}_C'], ang2bit(180 + (np.rad2deg(theta_c) - np.rad2deg(theta_b))))
            servo.MoveTo(servo_dict[f'F{k+1}_B'], ang2bit((np.rad2deg(theta_b)+90)))
            servo.MoveTo(servo_dict[f'F{k+1}_A'], ang2bit(360-(np.rad2deg(theta_a)+90)))

    val_motor += 1
             
while True:
    animate()
    time.sleep(1)
    print('testing')
    

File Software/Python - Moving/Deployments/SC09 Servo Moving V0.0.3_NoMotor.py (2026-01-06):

import sys
import trimesh
import pyautogui  
import numpy as np
import pyvista as pv
import matplotlib.pyplot as plt
from PyQt5.QtCore import QTimer
from pyvistaqt import QtInteractor
import matplotlib.colors as mcolors
from PyQt5.QtWidgets import QApplication, QMainWindow

# ================= File Imports ===================
from Claw_Functions import * # Home brew package
stl_path_A = r"..\..\..\Hardware\3D Models\Solidworks Servo\SC09\V0.2 - Bushing\Python_STL\SC09_Holder_Motor_A_Python.STL"
stl_path_B = r"..\..\..\Hardware\3D Models\Solidworks Servo\SC09\V0.2 - Bushing\Python_STL\SC09_Holder_Motor_B_Python_2.STL"
stl_path_C = r"..\..\..\Hardware\3D Models\Solidworks Servo\SC09\V0.2 - Bushing\Python_STL\SC09_Holder_Motor_C_Python.STL"
stl_path_T = r"..\..\..\Hardware\3D Models\Solidworks Servo\SC09\V0.2 - Bushing\Python_STL\SC09_Holder_Motor_T_Python.STL"

# ================= Parameters ===================

# Digit Lengths

A = 33.55 # bottom digit + motor A height
B = 43.55 # lower-middle digit + motor B height
C = 43.55 # upper-middle middle 2 digit + motor B height
T = 50 # top digit height

num_fingers = 5
Offset_R    = 75  # From origin (0,0,0)

R_tar       = 100  # Radius of target circle path 
H_tar       = 160  # Height of target circle path

delta_Z     = 20   # Dropping from path for reset 
points      = 100  # Number of points for path

minstep     = 0.5    # stepper motor step angle
speed       = 20   # Animation speed


Offset_theta_master = np.linspace(360,0,num_fingers+1)[0:num_fingers] # Flip the 0 and 360 to change direction
circle_tar = circle(R_tar, H_tar, np.linspace(0, 359, points))        # Builds target circle
fingertip_path = pathing(points, delta_Z,num_fingers,R_tar, H_tar)    # Builds a fingertip path
master_path = np.ones((num_fingers,3,points))                         # Allocates data for shifted finger path

path_load = int(points/num_fingers*(num_fingers-1))
master_path_load = np.concatenate((np.ones((num_fingers,1,path_load)), np.zeros((num_fingers,1,points - path_load))), axis=2)# Allocates data for shifted finger path, load path


############# PATTERNS #############
# # ROLLING PATTERN SHIFT
# for i in range(num_fingers):
#     """ Loop to adjust the finger path for each finger, offset by the points/fingers for even spacing."""
#     shifter = int(points / (num_fingers) * i)
#     shifted = np.roll(fingertip_path, shift=shifter, axis=1)
#     master_path[i] = shifted



# STAR PATTERN SHIFT (e.g. 1→3→5→2→4 for 5 fingers)
# Uses modular stepping to assign shifts in a star order instead of sequential order

step = 2                      # star step (works for odd num_fingers)
spacing = int(points / num_fingers)

order = []
current = 0
while current not in order:
    order.append(current)
    current = (current + step) % num_fingers

for shift_idx, finger_idx in enumerate(order):
    shifter = spacing * shift_idx
    shifted = np.roll(fingertip_path, shift=shifter, axis=1)
    master_path[finger_idx] = shifted
######################################

theta_reals = np.ones(3)*361.0 # random seed greater than any angle
theta_a = 361.0
theta_b = 361.0
theta_c = 361.0

step_counter = np.zeros(3)*0

t_a = []
t_b = []
t_c = []

val = 0
while True:

    if val == points:
        val = 0
        print('done')
        break

    for k in range(num_fingers):
        ### Finding angles and rebuilding fingers
        Xtar, Ytar, Ztar = master_path[k, :, int(val)] 
        Offset_theta = Offset_theta_master[k]
        Xtar_new, Ytar_new = rotate_point((0,0), (Xtar, Ytar),Offset_theta)
        Ztar_new = Ztar
        
        theta_reals = solve_thetas(Ztar, Ytar, Xtar, A, B, C, T,Offset_R)[0] 
        
        # checks for a change in angle based on the stepper motor step. makes it go from indefinite to a real world
        if theta_a == 361.0:
                theta_a = theta_reals[0]
                theta_b = theta_reals[1]
                theta_c = theta_reals[2]
        
        err = theta_reals[0] - theta_a
        if abs(np.rad2deg(err)) > minstep:
            nsteps = int(np.ceil(abs(np.rad2deg(err)) / minstep))
            step_change = np.sign(err) * nsteps * np.deg2rad(minstep)
            theta_a += step_change
            step_counter[0] += np.rad2deg(step_change)/minstep

        err = theta_reals[1] - theta_b
        if abs(np.rad2deg(err)) > minstep:
            nsteps = int(np.ceil(abs(np.rad2deg(err)) / minstep))
            step_change = np.sign(err) * nsteps * np.deg2rad(minstep)
            theta_b += step_change
            step_counter[1] += np.rad2deg(step_change)/minstep

        err = theta_reals[2] - theta_c
        if abs(np.rad2deg(err)) > minstep:
            nsteps = int(np.ceil(abs(np.rad2deg(err)) / minstep))
            step_change = np.sign(err) * nsteps * np.deg2rad(minstep)
            theta_c += step_change
            step_counter[2] += np.rad2deg(step_change)/minstep

        if k == 0:
            t_a.append(np.rad2deg(theta_a))
            t_b.append(np.rad2deg(theta_b))
            t_c.append(np.rad2deg(theta_b - theta_c))

    
    val += 1
                 

plt.figure()
plt.plot(range(points),t_a,'b',label = 'Motor A')
plt.plot(range(points),t_b,'orange',label = 'Motor B')
plt.plot(range(points),t_c,'green',label = 'Motor C')
plt.xlabel('point in operation')
plt.ylabel('degree in operation')

plt.legend()
plt.show()

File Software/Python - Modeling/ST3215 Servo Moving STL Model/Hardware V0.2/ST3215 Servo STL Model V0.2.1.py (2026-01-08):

import sys
import trimesh
import pyautogui  
import numpy as np
import pyvista as pv
import matplotlib.pyplot as plt
from PyQt5.QtCore import QTimer
from pyvistaqt import QtInteractor
import matplotlib.colors as mcolors
from PyQt5.QtWidgets import QApplication, QMainWindow

# ================= File Imports ===================
from Claw_Functions import * # Home brew package
stl_path_A = r"..\..\..\..\Hardware\3D Models\Solidworks Servo\ST3215\V0.2\Python_STL\ST3215_Holder_Motor_A_Python.STL"
stl_path_B = r"..\..\..\..\Hardware\3D Models\Solidworks Servo\ST3215\V0.2\Python_STL\ST3215_Holder_Motor_B_Python.STL"
stl_path_C = r"..\..\..\..\Hardware\3D Models\Solidworks Servo\ST3215\V0.2\Python_STL\ST3215_Holder_Motor_C_Python.STL"
stl_path_T = r"..\..\..\..\Hardware\3D Models\Solidworks Servo\ST3215\V0.2\Python_STL\ST3215_Holder_Motor_T_Python.STL"

# ================= Parameters ===================

# Digit Lengths

A = 40.7 # bottom digit + motor A height
B = 35.06 # lower-middle digit + motor B height
C = 57.7 # upper-middle middle 2 digit + motor B height
T = 50 # top digit height

num_fingers = 5
Offset_R    = 80  # From origin (0,0,0)

# R_tar       = 100  # Radius of target circle path 
# H_tar       = 190  # Height of target circle path

R_tar       = 100  # Radius of target circle path 
H_tar       = 170  # Height of target circle path

delta_Z     = 20   # Dropping from path for reset 
points      = 100  # Number of points for path

minstep     = 360/4096*10    # stepper motor step angle
speed       = 20   # Animation speed


Offset_theta_master = np.linspace(360,0,num_fingers+1)[0:num_fingers] # Flip the 0 and 360 to change direction
circle_tar = circle(R_tar, H_tar, np.linspace(0, 359, points))        # Builds target circle
fingertip_path = pathing(points, delta_Z,num_fingers,R_tar, H_tar)    # Builds a fingertip path
master_path = np.ones((num_fingers,3,points))                         # Allocates data for shifted finger path

path_load = int(points/num_fingers*(num_fingers-1))
master_path_load = np.concatenate((np.ones((num_fingers,1,path_load)), np.zeros((num_fingers,1,points - path_load))), axis=2)# Allocates data for shifted finger path, load path


############# PATTERNS #############
# # ROLLING PATTERN SHIFT
# for i in range(num_fingers):
#     """ Loop to adjust the finger path for each finger, offset by the points/fingers for even spacing."""
#     shifter = int(points / (num_fingers) * i)
#     shifted = np.roll(fingertip_path, shift=shifter, axis=1)
#     master_path[i] = shifted



# STAR PATTERN SHIFT (e.g. 1→3→5→2→4 for 5 fingers)
# Uses modular stepping to assign shifts in a star order instead of sequential order

step = 2                      # star step (works for odd num_fingers)
spacing = int(points / num_fingers)

order = []
current = 0
while current not in order:
    order.append(current)
    current = (current + step) % num_fingers

for shift_idx, finger_idx in enumerate(order):
    shifter = spacing * shift_idx
    shifted = np.roll(fingertip_path, shift=shifter, axis=1)
    master_path[finger_idx] = shifted
######################################

# Plot Settings
path_colors = ['tab:green','red','tab:orange','cyan','magenta']
joint_colors = ['tab:blue', '#BFBFBF', '#808080', '#404040', '#000000']
rose_color = 'grey'
tex_off = 10 # tet distance away from point
LW = 3 # Line width
PS = 10 # Point Size

vector_x = (1,0,0)
vector_y = (0,1,0)
vector_z = (0,0,1)
# ================= PyVista / Qt ===================

app = QApplication(sys.argv)
main_window = QMainWindow()
main_window.setGeometry(0, 0, pyautogui.size()[0]//2, pyautogui.size()[1])  # Left half of screen
main_window.setWindowTitle("Claw Animation")

plotter = QtInteractor(main_window)
main_window.setCentralWidget(plotter)
# viewing angle (all commented = trimetric)
# plotter.view_zx()  
# plotter.view_yx()
# plotter.view_yz()  

# === Stagnant Plots ===

# Plotting target Circle
circ_tar_points = np.column_stack((circle_tar[0], circle_tar[1], circle_tar[2]*np.ones(len(circle_tar[1]))))
plotter.add_lines(circ_tar_points, width=LW, color='black')

# Plotting Base Circle
base_circle = circle(Offset_R, 0, np.linspace(0,359,100))
base_circle_points = np.column_stack((base_circle[0], base_circle[1], base_circle[2]*np.ones(len(base_circle[1]))))
plotter.add_lines(base_circle_points, width=LW, color='blue')

# Directional rose
limits = H_tar
lims = np.array(range(-limits, limits))
rose_points = np.column_stack((lims, lims*0, lims*0)); plotter.add_lines(rose_points, width=LW, color=rose_color) # X
rose_points = np.column_stack((lims*0, lims, lims*0)); plotter.add_lines(rose_points, width=LW, color=rose_color) # Y
lims = np.array(range(0, limits))
rose_points = np.column_stack((lims*0, lims*0, lims)); plotter.add_lines(rose_points, width=LW, color=rose_color) # Z
plotter.show_bounds(location='back',
                    axes_ranges=[-limits, limits, -limits, limits, -limits/10, limits],
                    font_size=7,
                    xtitle='X',
                    ytitle='Y',
                    ztitle='Z')

# === Moving points ===

# Points
points_poly_dict = {}
points_actor_dict = {}
for p in range(num_fingers):
    for j in range(5):
        points_poly_dict[f'F{p}J{j}'] = pv.PolyData([0.0, 0.0, 0.0])
        if j != 4:
            points_actor_dict[f'F{p}J{j}'] = plotter.add_mesh(points_poly_dict[f'F{p}J{j}'], color=joint_colors[j], point_size=PS, render_points_as_spheres=True)
        else:
            points_actor_dict[f'F{p}J{j}'] = plotter.add_mesh(points_poly_dict[f'F{p}J{j}'], color=path_colors[p], point_size=PS, render_points_as_spheres=True)
            
# Lines - Fingers and Paths lines_poly_dict[f'P{k}'].points = np.column_stack((master_path_plot[0], master_path_plot[1], master_path_plot[2]))
            
lines_poly_dict = {}
lines_actor_dict = {}
for p in range(num_fingers):
    lines_poly_dict[f'F{p}'] = pv.PolyData(np.array([[0.0,0.0,0.0]]*5), lines=np.hstack([[5, *range(5)]]))
    lines_actor_dict[f'F{p}'] = plotter.add_mesh(lines_poly_dict[f'F{p}'], color='black', line_width=LW)

    lines_poly_dict[f'P{p}'] = pv.PolyData(np.array([[0.0,0.0,0.0]]*points), lines=np.hstack([[points, *range(points)]]))
    lines_actor_dict[f'P{p}'] = plotter.add_mesh(lines_poly_dict[f'P{p}'], color=path_colors[p], line_width=LW)


### STL (testing)
motor_poly_dict = {}
motor_actor_dict = {}
opacity_stl = 1
opacity_color = "lightgray"
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

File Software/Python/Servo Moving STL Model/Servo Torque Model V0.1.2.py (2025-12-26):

import numpy as np
import matplotlib.pyplot as plt


# Digit Lengths
A = 33.55 # mm, bottom digit + motor A height
B = 43.55 # mm, lower-middle digit + motor B height
C = 43.55 # mm, upper-middle middle 2 digit + motor B height
T = 43.55    # mm, top digit height

titles = ['Motor C Torque', 'Motor B Torque', 'Motor A Torque']

# individual sections
A = A/1000 # m, bottom digit + motor A height
B = B/1000 # m, lower-middle digit + motor B height
C = C/1000 # m, upper-middle middle 2 digit + motor B height
T = T/1000 # m, top digit height


weight_bearing = 10 / 1000 # kg
weight_motor =   21 / 1000 # kg

buffer = 5
Holder_Motor_B_Weight = 17 / 1000 + buffer/1000 #kg
Holder_Motor_C_Weight = 15 / 1000 + buffer/1000  #kg
Holder_Motor_T_Weight = 8  / 1000 + buffer/1000  #kg

# weights to move
W_plate =  0  /  2.20462 # kg, only 4 fingers will hold at a time
W_plate = W_plate/4 # kg, only 4 fingers will hold at a time

Holder_Motor_C_Weight2Move = [0, 0, Holder_Motor_T_Weight+W_plate]
Holder_Motor_B_Weight2Move = [0, Holder_Motor_C_Weight + weight_motor + weight_bearing, Holder_Motor_T_Weight+W_plate]
Holder_Motor_A_Weight2Move = [Holder_Motor_B_Weight + weight_motor + weight_bearing, Holder_Motor_C_Weight + weight_motor + weight_bearing, Holder_Motor_T_Weight+W_plate]

# Lengths to move
Holder_Motor_C_Length2Move = [0,0,T]
Holder_Motor_B_Length2Move = [0,B,T]
Holder_Motor_A_Length2Move = [C,B,T]

lengths = np.array([Holder_Motor_C_Length2Move,Holder_Motor_B_Length2Move,Holder_Motor_A_Length2Move])
weights = np.array([Holder_Motor_C_Weight2Move,Holder_Motor_B_Weight2Move,Holder_Motor_A_Weight2Move])
moments = lengths*weights
moments = sum(moments.transpose()) # combines to find a single moment, order of C, B, A

# Overall
# The torque (stalled) is 2.3kg.cm@6V
# The torque (moving)  is 0.7kg.cm@6V
kgcm2mNm = 98.0665 # N•m / Kg•cm
motor_torque = 1.29 #Kg•cm

motor_torque = motor_torque * kgcm2mNm / 1000 #N·m, Motor Strength
K_constant = 1.4  # in•lbf, Spring Strength
K_array = np.ones(3)*K_constant

inlbf2Nm = 1 / 8.85075 # in•lbf / N•m
theta_deflection = 270
K_array = K_array*inlbf2Nm / theta_deflection  # N•m/theta
G = 9.8 # m /s^2

fig, axs = plt.subplots(3,1,sharex = True,figsize=(6, 9))
fig.canvas.manager.window.move(500,0)

################### Motor C ###################

# All points - plotted
x = np.linspace(0,180,361)

for i in range(0,len(axs.reshape(-1))):
    K = K_array[i]
    Mom = moments[i]
    weight_torque_array = []
    spring_torque_array = []
    motor_torque_array = []    
    for k in range(0,len(x)):    
        theta = x[k]
        weight_torque = Mom*G*np.cos(np.deg2rad(theta)) # (m)*(m/s^2)*kg = m*N
        spring_torque = K*theta
        weight_torque_array.append(weight_torque)
        spring_torque_array.append(spring_torque)
        motor_torque_array.append(motor_torque)    

    axs[i].plot(x,motor_torque_array,label = 'Motor', c = 'k')
    axs[i].plot(x,-np.array(motor_torque_array), c = 'k')
    axs[i].plot(x,weight_torque_array,label = 'Weight',c='b',alpha = 0.25)
    axs[i].plot(x,spring_torque_array,label = 'Spring',c='r',alpha = 0.25)
    axs[i].plot(x,x*0,'--k')
    axs[i].plot(x,np.array(weight_torque_array) + np.array(spring_torque_array),label = 'Total',c='m')
    axs[i].set_title(titles[i])

axs[0].set_ylabel('Torque / N•m')
axs[1].set_ylabel('Torque / N•m')
axs[2].set_ylabel('Torque / N•m')

axs[2].set_xlabel('Theta / $\Theta$')
axs[2].set_xlim([0,180])


axs[0].legend()
plt.show()

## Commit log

2025-10-27 Ball-and-stick Model Update
    Python code for ball-and-stick model of n-fingers rotating around the origin has been created. The code takes physical constants (joint lengths) and variables (target point) and outputs the angles (f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
    [Assem1.SLDASM, Motor A Back Block.STL]
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2025-10-30 Organizational Update
    - Realized that my servo motor models were probably never going to be used by anyone but me, so I deleted them from the repor.
    - Started transferring my python models to using PyVista instead of Matplotlib. PyVista is WAY better at handling meshes/3D models - which is needed if I want to add ghost STLS into the ball-and-stic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
    [AAA Test Rig.SLDASM, All.SLDASM, Assem1.SLDASM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]
2025-11-05 Progress update
    Continuing to convert ball and stick models to stl moving models
    [AAA Test Rig.SLDASM, Bearing.SLDPRT, Motor A + Base.SLDPRT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]
2025-11-12 Pyvista model complete
    Phew that was a lot of thinking in 3D space. I hope the comments are detailed enough. Now that I have the model working, I can finalize the 3d models in solidworks!
    [Motor B.STL, Motor C + bearing.SLDASM, Motor C + bearing.STL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]
2025-11-15 model updates
    [Assem1.SLDASM, Bearing Insert.SLDPRT, Bearing Insert.STL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]
2025-12-23 Lots of changes, cant count
    [28BYJ-48+ULN2003A Step Motor Module.SLDPRT, 28BYJ-48+ULN2003A Step Motor Module.stp, 28BYJ-48.SLDPRT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]
2025-12-26 temp update
    [Assembly_Main.SLDASM, Base_Test.SLDASM, Holder_Motor_A.SLDPRT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]
2025-12-27 laptop update - renaming files
    [SC09-SERVO.SLDPRT, SC09-SERVO.step, SC09_ARM.SLDASM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]
2025-12-28 desktop update
    [28BYJ-48+ULN2003A Step Motor Module.SLDPRT, 28BYJ-48+ULN2003A Step Motor Module.stp, 28BYJ-48.SLDPRT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]
2025-12-28 readme update
    [9271K382_Torsion Spring.SLDPRT, Bushing.SLDPRT, Bushing_9.6x12.7x13.4.SLDPRT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]
2025-12-29 Initial Spring Modeling
    [9271K382_Torsion Spring.SLDPRT, SC09-SERVO.SLDPRT, SC09_Holder_Motor_A.SLDPRT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]
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2025-12-30 laptop update
    [9271K382_Torsion Spring.SLDPRT, Bushing.SLDPRT, SC09-SERVO.SLDPRT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]
2025-12-31 lapotop update - need to align stls
    [9271K382_Torsion Spring.SLDPRT, SC09_Assembly_AB.SLDASM, SC09_Assembly_BC.SLDASM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]
2026-01-01 almost final build
    [9271K382_Torsion Spring.SLDPRT, SC09_Assembly_AB.SLDASM, SC09_Assembly_ABC.SLDASM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]
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2026-01-01 well this is awesome
    I can get the motor to move!
    [pyvenv.cfg]
2026-01-02 3d printing start
    [9271K382_Torsion Spring.SLDPRT, SC09_Assembly_Main.SLDASM, SC09_Holder_Motor_A.SLDPRT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]
2026-01-02 3d printing updates
    [SC09_Assembly_Main.SLDASM, SC09_Holder_Motor_A.SLDPRT, SC09_Holder_Motor_A.STL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]
2026-01-03 printing updates
    [SC09_Assembly_Claw.SLDASM, SC09_Assembly_Finger.SLDASM, SC09_Assembly_Main.SLDASM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]
2026-01-04 Large print update
    [SC09_Holder_Motor_B_Cut-1.SLDPRT, SC09_Holder_Motor_B_Cut-2.SLDPRT, SC09_Holder_Motor_B_Cut-2.STL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]
2026-01-06 SC-09 update
    Built one finger useing SC-09 motors. Although cool, I dont think its feasilbe with the step angle (which is NOT 0.293. its 0.293*15 == 4.4, which is super jumpy). Considering using ST3215 motors now
    [Bushing.SLDPRT, SC09-SERVO.SLDPRT, SC09_Assembly_Claw.SLDASM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]
2026-01-07 ST3215 motor models
    [Bushing.SLDPRT, SC09-SERVO.SLDPRT, SC09_Assembly_Claw.SLDASM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]
2026-01-07 more model updates
    [ST3215_Holder_Motor.SLDPRT, ST3215_Holder_Motor_A.SLDPRT, ST3215_Holder_Motor_A_Python.SLDASM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]
2026-01-08 nothin nnew just updating fiele poatha
    [ST3215_Holder_Motor_B.SLDPRT, ST3215_Holder_Motor_B_Python.SLDASM, STM3215_Assembly_Finger.SLDASM]
2026-01-08 Set a different configuration to motor B in V0.2 of ST3215
    [ST3215.SLDPRT, ST3215.step, ST3215_Holder_Arm.SLDPRT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]
2026-01-09 starting to 3d print
    [ST3215_Holder_Arm.SLDPRT, ST3215_Holder_Motor_B_Python.SLDASM, ST3215_Holder_Motor_B_Python.STL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]
2026-01-10 ITS PRINTING TIME
    [ST3215_Holder_Arm.SLDPRT, ST3215_Holder_Motor_A_Python.SLDASM, ST3215_Holder_Motor_A_Python.STL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]
2026-01-12 model update
    [STM3215_Assembly_Claw.SLDASM, STM3215_Assembly_Finger.SLDASM]
2026-01-12 Added Items to model
    [Baseball.stl, Plate_1.SLDPRT, Plate_1.STL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]
2026-01-13 File organization
    [28BYJ-48+ULN2003A Step Motor Module.SLDPRT, 28BYJ-48+ULN2003A Step Motor Module.stp, 28BYJ-48.SLDPRT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]
2026-01-13 Code cleanup
    [Baseball.stl, Plate_1.SLDPRT, Plate_1.STL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]
2026-01-15 GGG
    1`fcxdcfvs
    [ST3215.SLDPRT, ST3215_Assembly_Finger.SLDASM, ST3215_Assembly_Holder_Motor.SLDASM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]
2026-01-18 v0.3 claw update
    [ST3215_Arm_A.SLDPRT, ST3215_Arm_A.STL, ST3215_Assembly_Finger.SLDASM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]
2026-01-22 V0.4 woooo
    [ST3215.SLDPRT, ST3215.step, ST3215_Arm_A.SLDPRT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]
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2026-03-12 Update - need to add springs
    [Base_Assembly.SLDASM]
2026-03-13 bought some springs yo
    [12V_Base_Connector.SLDPRT, 12V_Base_Connector.STL, 12V_Supply.SLDPRT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]
2026-03-16 start to spring models
    [ST3215_Assembly_ALLCOMPLETE.SLDASM, ST3215_Assembly_Claw.SLDASM, ST3215_Assembly_Electronics_Bay.SLDASM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]
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
